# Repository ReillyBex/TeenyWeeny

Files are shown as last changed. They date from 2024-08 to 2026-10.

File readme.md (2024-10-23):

# TeenyWeeny

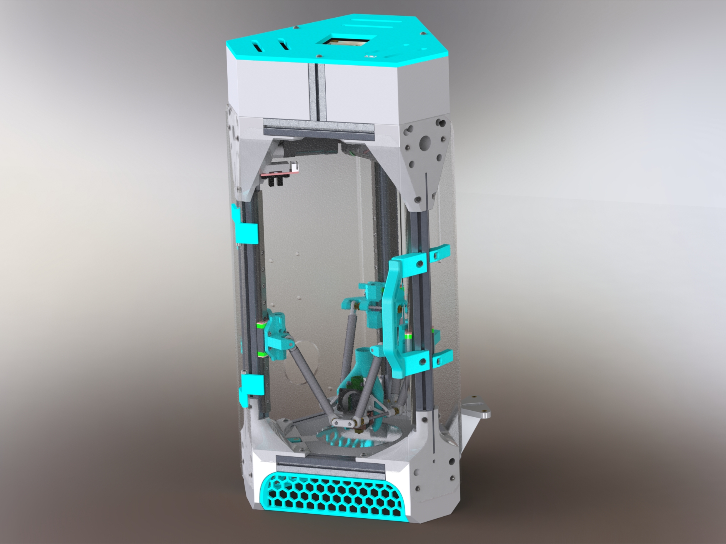
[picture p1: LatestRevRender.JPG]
Printer Render


A small form factor delta printer designed to be rigid and compact. I created most of the parts myself, but I also modified existing designs in the community. Credit is given below to the models I either used directly or modified. 

Print volume is 75mm diameter circle x ~120mm in Z. Arm Length is 85mm. Delta Radius is 38.1mm, Print_Radius is 37mm. Belt tension on the long side of the belt should be about 174Hz to reach spec load at spec length. Example graphs from Input Shaper are included below. 40k acceleration MZV is not too shabby! Smol delta go brrrrrrrr.          

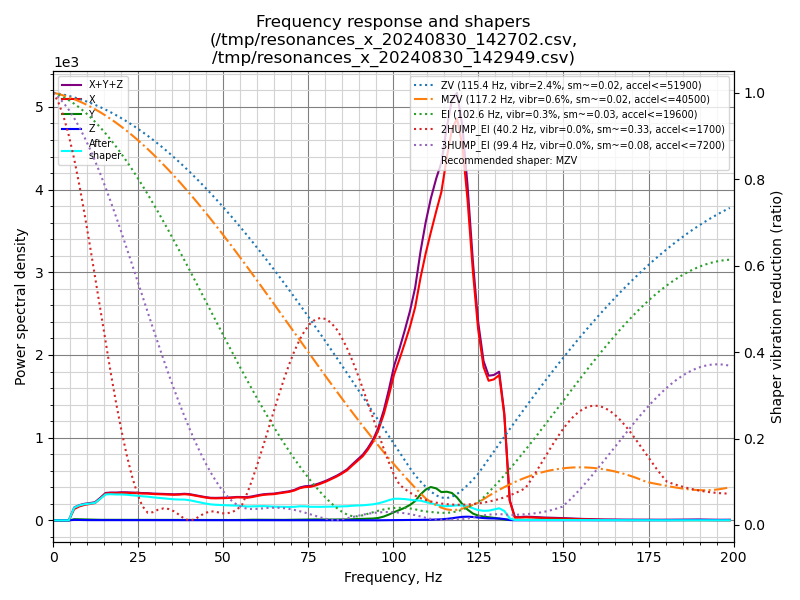
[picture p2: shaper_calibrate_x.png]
Shaper X
    
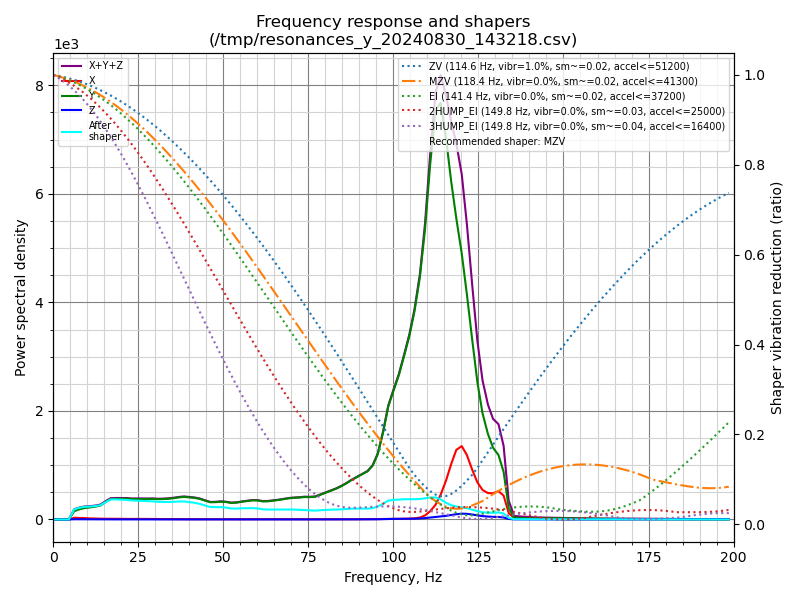
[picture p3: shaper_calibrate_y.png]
Shaper Y
          

Credit to models used in the CAD:  
https://www.printables.com/model/875189-min_sb01_80 for the stock effector design.    
https://github.com/clee/VoronBFI for the base BZI model I modified for use in Teeny Weeny.       
https://github.com/ApexArray/ApexClips for the Apex Clips used in the carriages.  
The MP Jet models are courtesy of Colphaer and Burgo, find them pinned in the Rolohaun discord Delta channel. 

Shoutout to models and designs used in the build:      
https://www.vorondesign.com/ for their designs and the starting point for pretty much all my work.      
https://github.com/KayosMaker/1515PanelClips for the 1515 panel clips.        
https://www.printables.com/model/857334-min-micro-delta-3d-printer for their work on small deltas and the discord community that helped me refine my design.      
https://www.printables.com/model/530995-v0-1515-extrusion-slot-cover/files for the 1515 slot covers.

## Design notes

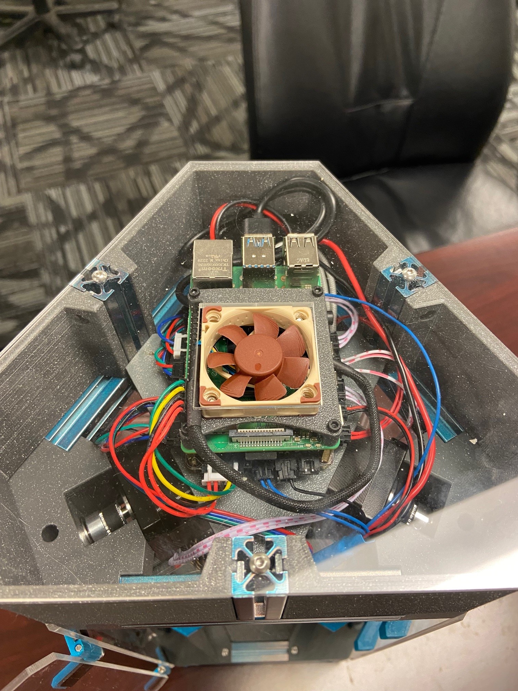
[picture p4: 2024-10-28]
Electronics Layout.jpg

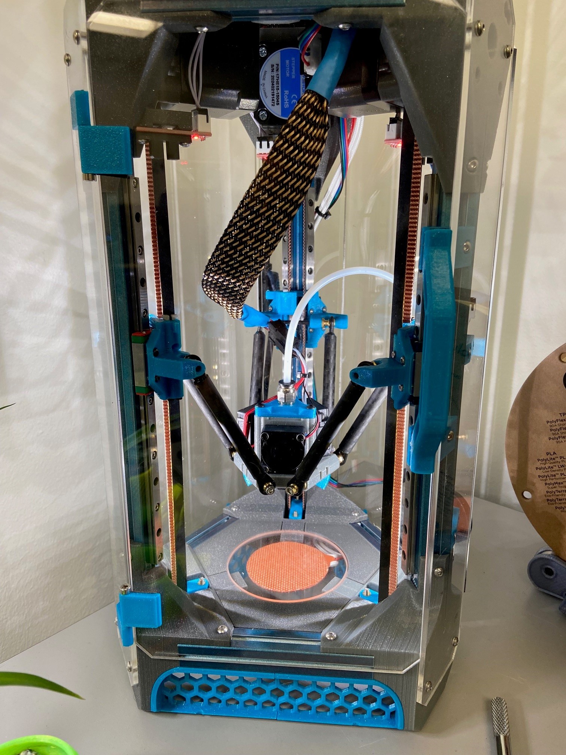
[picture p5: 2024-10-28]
Stock Config.jpg

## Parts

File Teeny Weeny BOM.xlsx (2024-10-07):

Teeny Weeny | Estimated Price | AliExpress | Amazon
Frame
3 x 250mm 1515 aluminum extrusion (might need to cut down from 300mm) | $15.00 |  | Amazon.com: MakerBeam XL Clear Anodized Beams 300x15x15mm 4 Pieces : Industrial & Scientific (https://www.amazon.com/MakerBeam-XL-Anodized-300x15x15mm-Pieces/dp/B06XJ4F9WW?hvadid=79852084166625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)
6 x 100mm 1515 aluminum extrusion | $25.00 |  | Amazon.com: MakerBeam XL Clear Anodized Beams 50x15x15mm (103374) 4 Pieces x 2 and 100x15x15mm (103385) 4 Pieces x 2 : Industrial & Scientific (https://www.amazon.com/MakerBeam-XL-Anodized-50x15x15mm-100x15x15mm/dp/B06XJ4FZ12?adgrpid=1341404752136090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)
3 x 50mm 1515 aluminum extrusion
Motion
POWGE GT2 6mm wide Belt 4 meters |  | https://s.click.aliexpress.com/e/_DBPBTXJ (https://www.aliexpress.com/item/902692789.html?pdp_ext_f=%7B%22sku_id%22%3A%2266484598505%22%7D) | Amazon.com: 5M GT2 Timing Belt, Upgrade Non-Slip Version, Width 6mm, Fit for 3D Printer and Most Belt Driven Printers : Automotive (https://www.amazon.com/dp/B08R93QQ8Z?ref=ppx_yo2ov_dt_b_product_details&th=1)
3 x 16T 5mm Bore Pulley |  | https://www.aliexpress.us/item/2251832808824051.html
6 x F623 flanged bearings (idler bearing stacks)
3 x F695 Bearings (Pack of 10 Raindew Recommended ) |  | https://s.click.aliexpress.com/e/_DeHjOz3
3 x Nema17 Any you prefer ( 48mm Max ) |  | https://s.click.aliexpress.com/e/_DmCB9SX | https://www.amazon.com/dp/B0B38GHRH8?psc=1&ref=ppx_yo2ov_dt_b_product_details
12 x MP Jet Joints (you need 2 packs of 6) |  |  | https://mpjet.com/shop/gb/ball-7-mm-dia/1286-375-ball-link-v1-type-7-mm-dia-m33-short.html
3 x 70mm length 3mm diameter carbon fiber rods for carriage joint pins (cut from longer rod) |  |  | Amazon.com: MECCANIXITY Carbon Fiber Rod, 3mm x 100mm for RC Plane DIY Tool Wing Tube Quadcopter Arm, Pack of 12 : Industrial & Scientific (https://www.amazon.com/dp/B0B6BWDQ67?ref=ppx_yo2ov_dt_b_product_details&th=1)
6 x 6mm ID 8mm OD 65mm long carbon fiber tubes for arms (Cut from longer tube) |  |  | Amazon.com: ARRIS 330mm 6mm x 8mm x 330mm Carbon Fiber Tubes Matte Surface 3K Roll Wrapped 100% Pure Pultruded Carbon Tubing for Quadcopter Multicopter (2PCS) : Industrial & Scientific (https://www.amazon.com/dp/B09X2Z385R?ref=ppx_yo2ov_dt_b_product_details&th=1)
6 x MGN7H 200mm Z2 preload linear rails |  | Linear Guide MGN7C MGN7H Rail Kit 440C Stainless Steel Miniature Slide Guideway Motion 1pc Rail with Carriage Set CNC 3D Printer - AliExpress 13 (https://www.aliexpress.us/item/3256801304880853.html?scm_id=1007.22922.271278.0&scm-url=1007.22922.271278.0)
Hardware ( Working in Progress )
82 - M3 x 8mm (a pack of 100 will probably be enough) |  | https://boltdepot.com/Metric_socket_cap_Stainless_steel_18-8_(A-2)_3mm_x_0.5mm
40 - M3 nuts (for screws into extrusion slots)
12 - M3 x 20mm for motor mounting
6 - M3 x 25mm for Effector Arms (Must be SHCS for clearances to work)
8 - M3x30mm for tensioners and door
Heatsets M3 X D5.0 X L4.0 ( I order 300 because you always need them :) ) |  | https://s.click.aliexpress.com/e/_DdVhkQl | uxcell knurled Insert Nuts, 120Pcs M3 x 4mm L x 5mm OD 3D Printing Brass Nuts Female Threaded Inserts Brass Heat Set Insert Embedment Nut: Amazon.com: Industrial & Scientific (https://www.amazon.com/dp/B09MCWTBCC?psc=1&ref=ppx_yo2ov_dt_b_product_details)
6 - M3NS square nuts for effector |  |  | HWM3D 25pcs M3nS - Thin M3 Square Nuts for PRUSA 3D Printers - A2 Stainless Steel - DIN562, Thickness 1.8mm: Amazon.com: Industrial & Scientific (https://www.amazon.com/dp/B0D6SP881V?ref=ppx_yo2ov_dt_b_product_details&th=1)
6 - M3 0.5mm shim washers for idler bearing stacks
Rubber feet |  |  | https://www.amazon.com/dp/B088HGQSZT?psc=1&ref=ppx_yo2ov_dt_b_product_details
M2.5 standoffs and fasteners for electornics and effector |  |  | DYWISHKEY 320 Pieces Male Female Hex Brass Spacer Standoff Screw Nut Assortment Kit (M2.5): Amazon.com: Industrial & Scientific (https://www.amazon.com/dp/B07MW5P8JH?ref=ppx_yo2ov_dt_b_product_details&th=1)
66 - M2 x 6 SHCS for rails and carriages |  | Bolt Depot - Metric socket cap, Stainless steel 18-8 (A-2), 2mm x 0.4mm (https://boltdepot.com/Metric_socket_cap_Stainless_steel_18-8_(A-2)_2mm_x_0.4mm)
58 - M2 nuts for rails
Extruder + Hotend
Dual Gear Extruder HGX-LITE-Extruder |  | https://s.click.aliexpress.com/e/_Dl5DEIV
Clone Bambu Hotend |  | https://s.click.aliexpress.com/e/_DFTGhVP
PC4-M10 pneumatic fitting |  | Amazon.com: PC4-M10 Male Straight Pneumatic PTFE Tube Push In Quick Fitting Connector for E3D-V6 Long-Distance Bowden Extruder 3D Printer (Pack of 10pcs) : Industrial & Scientific (https://www.amazon.com/dp/B07S1GLM8R?psc=1&ref=ppx_yo2ov_dt_b_product_details)
PC4-M6 pneumatic fitting |  | Amazon.com: PC4-M6 Straight Fitting 4mm Thread M6 Connector for 3D Printer (Pack of 10 pcs) : Industrial & Scientific (https://www.amazon.com/dp/B08BKJ1N6L?psc=1&ref=ppx_yo2ov_dt_b_product_details)
Nema 14 pancake stepper for extruder |  |  | Amazon.com: FYSETC 3D Printer Parts 36mm Motor Extruder Stepper Motor 1.8 Angle 0.35A 2 Phase Round Body with 47.2in Cable for Sherpa Mini/Orbite Extruder Ender 3 Pro V2 /Voro 2.4/Positro Project Accessories : Industrial & Scientific (https://www.amazon.com/dp/B099JMJNH2?psc=1&ref=ppx_yo2ov_dt_b_product_details)
BED
Borosilicate glass disk | $23.18 | https://www.mcmaster.com/8477K88
24V 30W 50mm diameter silicone heating pad (Keenovo custom order) | $50.00 | Contact Us_Custom Flexible Heating Elements, Silicone Heater, Kapton Heater-Keenovo.com (https://www.keenovo.com/contact/us.html)
Electronics
24v 6amp AC Adapter |  | https://s.click.aliexpress.com/e/_DdGr7Hd
Optical Endstop |  | https://s.click.aliexpress.com/e/_DF2pjnD
BTT Pico |  | https://s.click.aliexpress.com/e/_DClRklL | Amazon.com: BIGTREETECH SKR PICO V1.0 Control Board Integrated 4 Axis TMC2209 UART Stepper Motor Driver Compatible with Raspberry Pi Online Printing for Voron V0 V0.1 3D Printer Motherboard : Industrial & Scientific (https://www.amazon.com/dp/B09MYKL9MP?ref=ppx_yo2ov_dt_b_product_details&th=1)
SBC (any Raspberry Pi should work)
2510 5v ball bearing fan for hotend ( I recommend Delta )
3010 24v GDstime Layer Cooling |  | https://s.click.aliexpress.com/e/_DCciStb
2x8 molex microfit 3.0 connector for effector umbilical |  |  | Molex Micro-Fit 3.0 Dual Row (8 Circuits) Male & Female Receptacle Plug, w/Terminal sockets, (Pack of 1 Complete Set): Amazon.com: Industrial & Scientific (https://www.amazon.com/dp/B07997NH2Q?psc=1&ref=ppx_yo2ov_dt_b_product_details)
4010 fan for Raspberry Pi cooling (optional) |  |  | Amazon.com: Noctua NF-A4x10 5V, Premium Quiet Fan, 3-Pin, 5V Version (40x10mm, Brown) : Electronics (https://www.amazon.com/Noctua-Cooling-Bearing-NF-A4X10-FLX-5V/dp/B00NEMGCIA)
CPAP Driver Board (IF using CPAP toolhead) |  | High Speed Turbine Fan with Nidec Brushless Motor and Built-in Drive for Sweeper and Vacuum Cleaner - AliExpress 1420 (https://www.aliexpress.us/item/3256805751725080.html)
Roborock Blower Fan |  | Ldee5bgs173tw01|roborock S50 S51 S52 S55 Motor Replacement - Xiaomi Mi Robot Sdjqr01rr Parts (aliexpress.us) (https://www.aliexpress.us/item/3256804036608448.html)
TOTAL CAD | $113.18
TOTAL USD | #NAME?

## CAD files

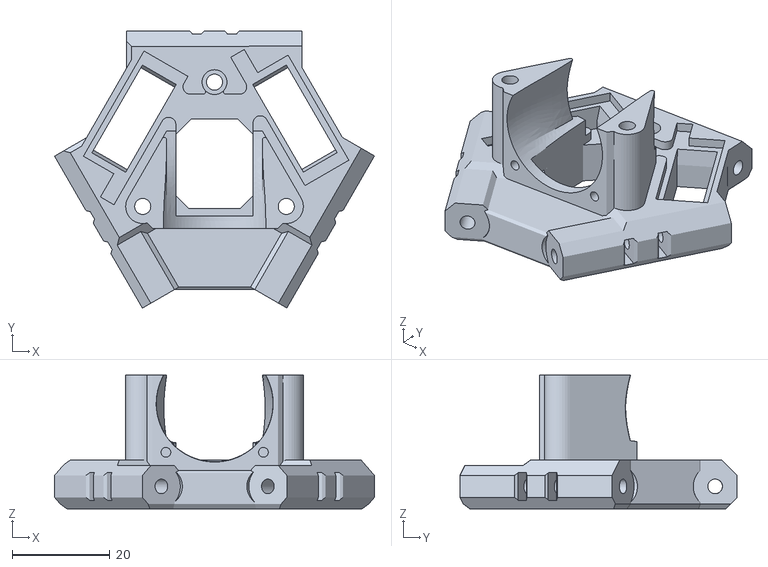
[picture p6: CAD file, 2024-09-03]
STL/Bambu SB Effector/MIN_EFFECTOR_M3X30_3010_BAMBU_MainPlate.STL
65.6 x 56.9 x 27.4

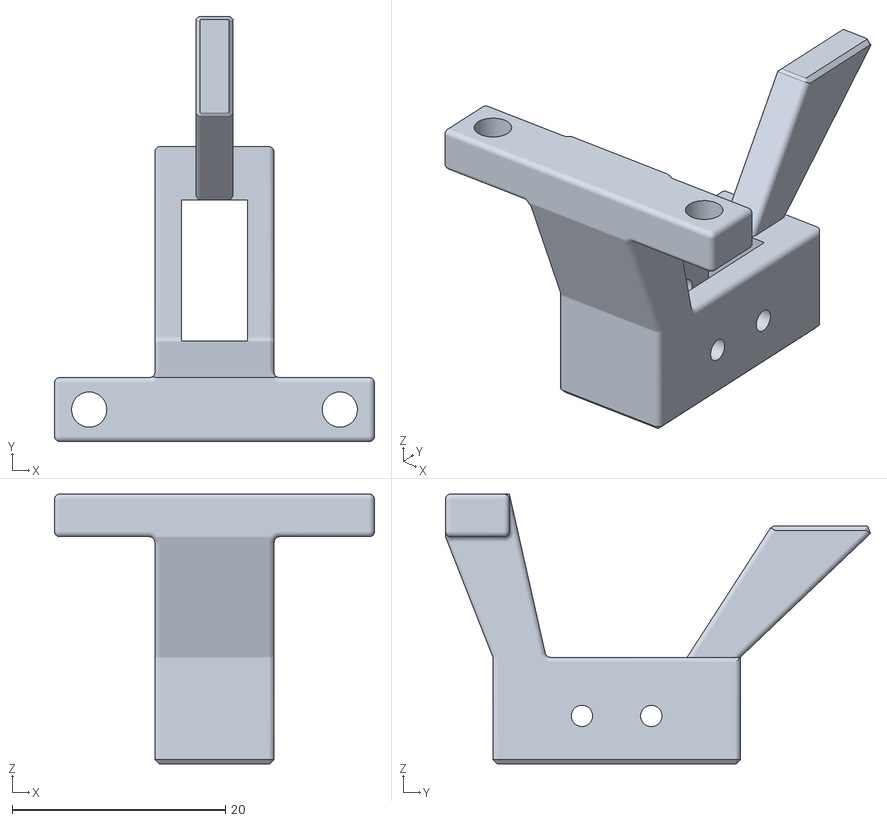
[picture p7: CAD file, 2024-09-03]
STL/Bambu SB Effector/Probe_Mount.STL
30.0 x 39.9 x 25.3

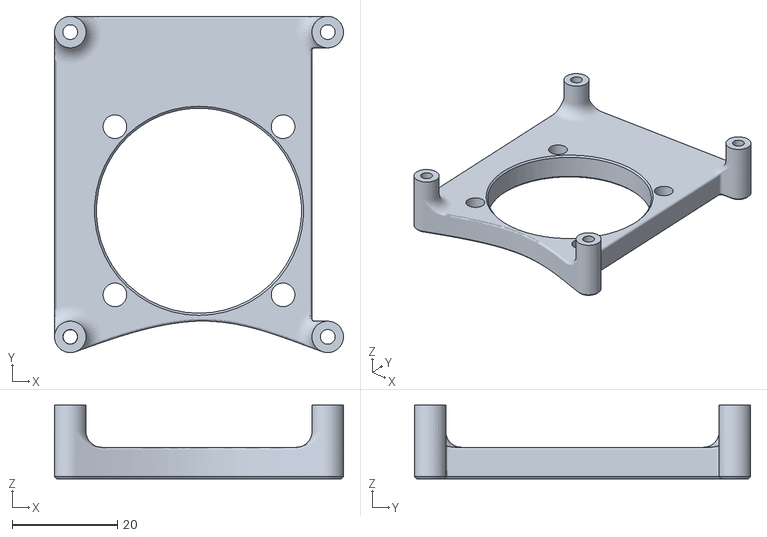
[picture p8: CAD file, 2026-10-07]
STL/Electronics/4010_RPi_FanMount_Heatset.STL
55.0 x 64.0 x 14.0

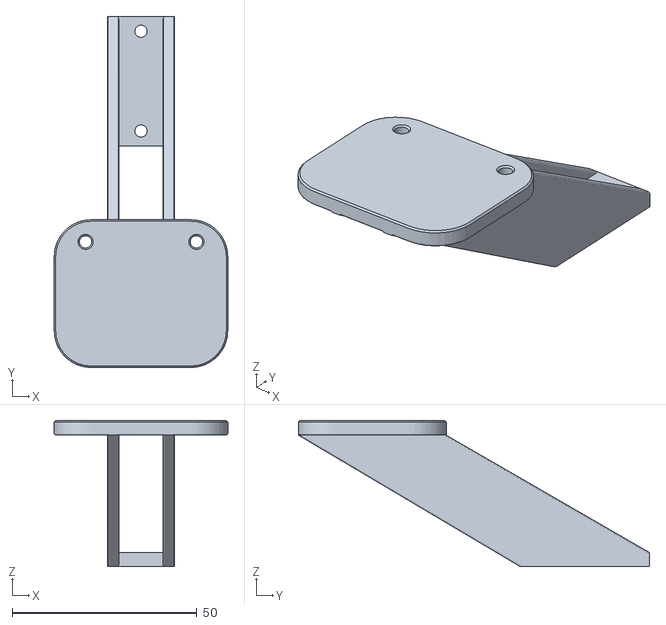
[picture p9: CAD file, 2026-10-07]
STL/MISC/Jetpack_Mount_Taller.STL
47.0 x 95.0 x 39.5

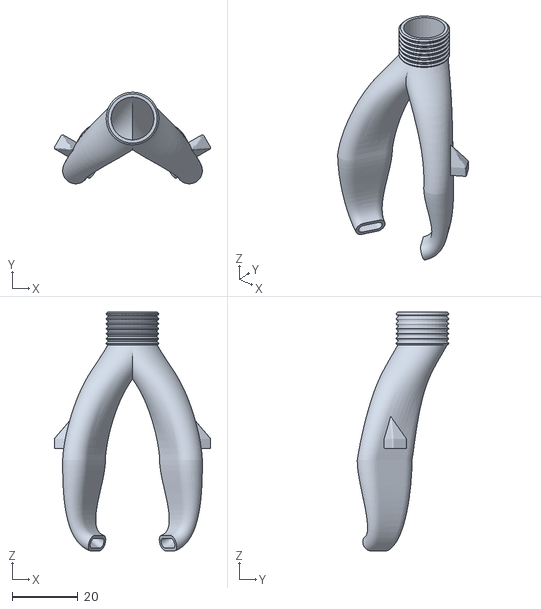
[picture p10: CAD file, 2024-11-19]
STL/Motion/CPAP Ducts.STL
47.5 x 27.8 x 72.6

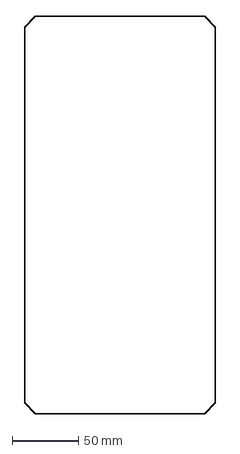
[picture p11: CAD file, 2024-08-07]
STL/Panel DXFs/Side_Door_Panel_x3.DXF
143.8 x 299.2 mm

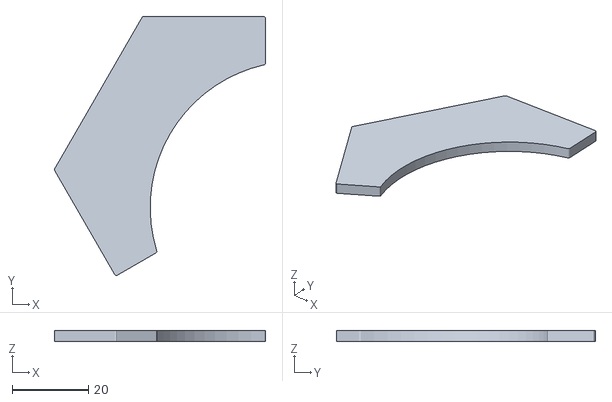
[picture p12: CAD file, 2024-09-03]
STL/Panels/BedPanel_1_x3.STL
55.3 x 67.8 x 3.00

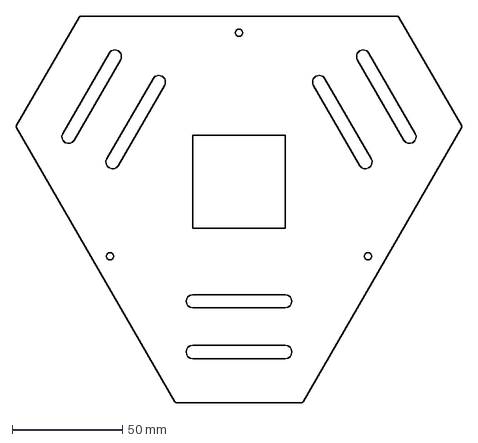
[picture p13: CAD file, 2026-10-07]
STL/Panels/Panel DXFs/TopPanel_Cutouts.DXF
201.8 x 175.1 mm

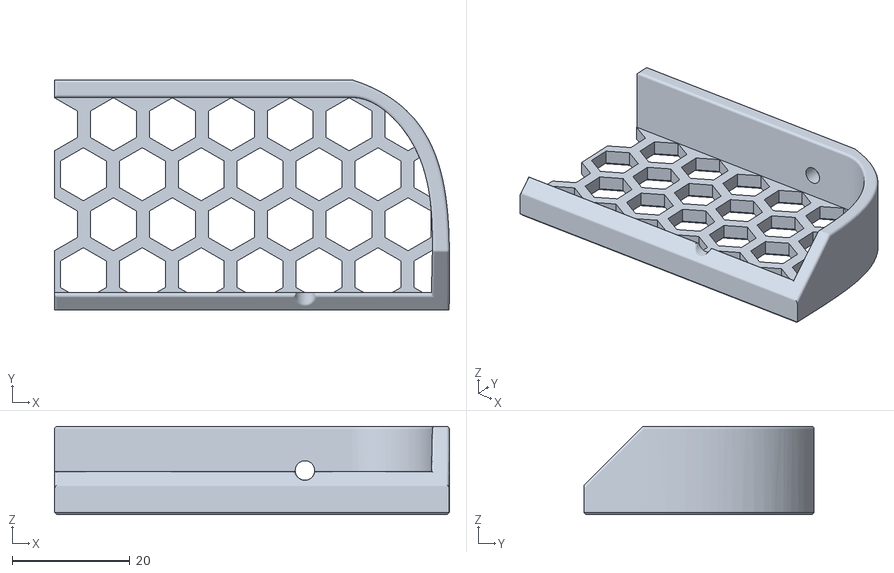
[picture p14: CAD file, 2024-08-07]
STL/Skirts/[a]_Skirt_Half_x3.STL
67.0 x 39.1 x 15.0

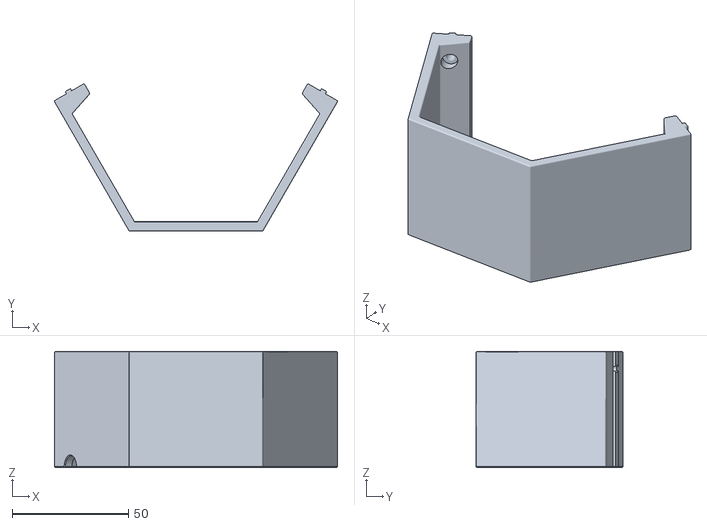
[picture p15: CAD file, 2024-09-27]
STL/Structure/TopHat_CPAP_Wires.STL
121.9 x 63.3 x 50.0

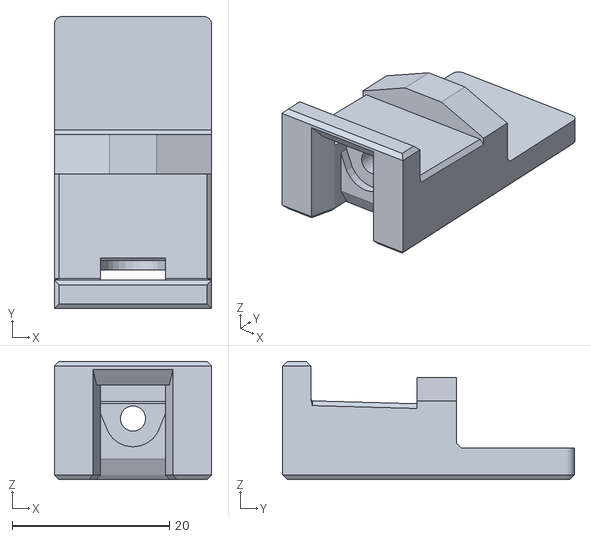
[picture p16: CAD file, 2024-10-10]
STL/Tools/MP Jet Joint Filing Jig V2.stl
20.0 x 37.1 x 15.0

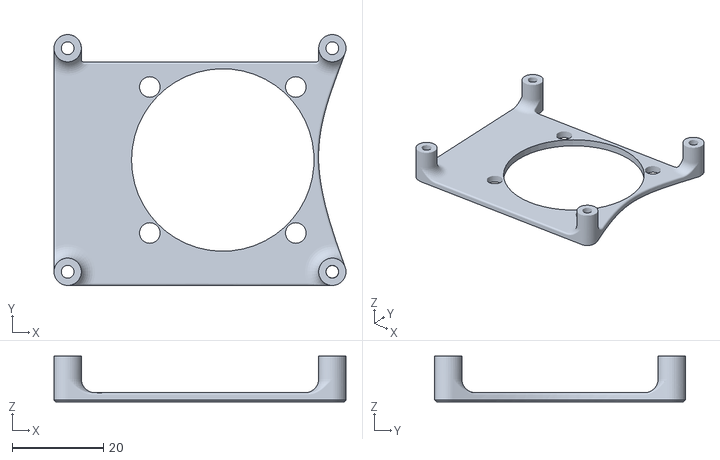
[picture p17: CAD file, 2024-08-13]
STL/Electronics/4010_RPi_FanMount.STL
64.0 x 55.0 x 10.0

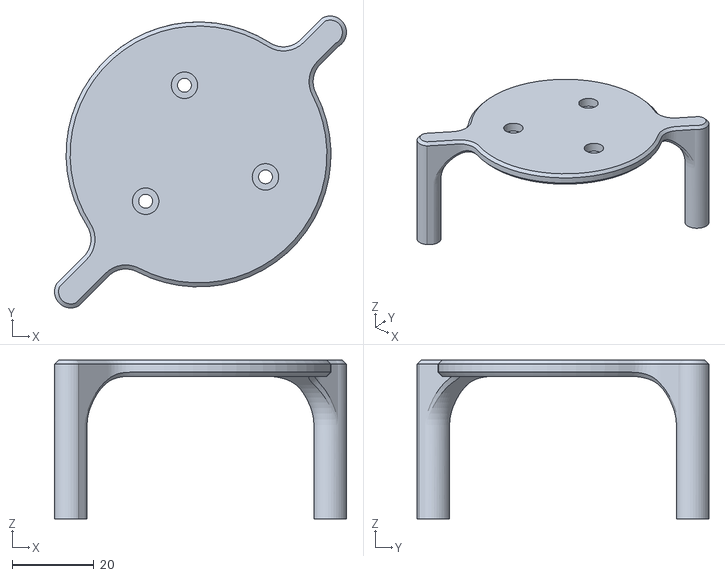
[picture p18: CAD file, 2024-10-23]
STL/MISC/mount_plate_no_logo.STL
71.6 x 71.6 x 39.0

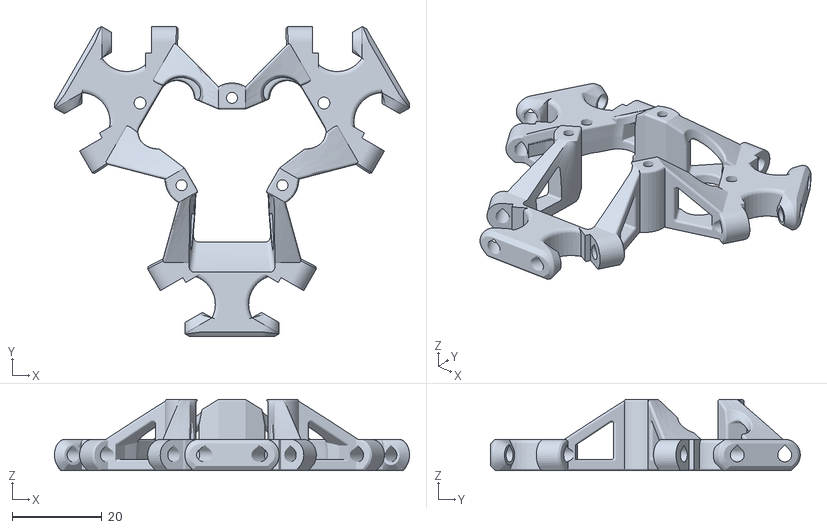
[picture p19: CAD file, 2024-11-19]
STL/Motion/CPAP Effector Plate.STL
79.2 x 69.1 x 15.9

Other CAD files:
STL/Panels/BedPanel.STL
STL/Panels/Panel DXFs/CPAP_Side_Panel.DXF
STL/Skirts/[a]_Skirt_Half_Mirror_x3.STL
STL/Structure/Foot_Double_Cable_Routing.STL
STL/Bambu SB Effector/MIN_EFFECTOR_M3X30_3010_BAMBU_CoolingDucts.STL
STL/Bambu SB Effector/MIN_EFFECTOR_M3X30_3010_BAMBU_HotendMount.STL
STL/Bambu SB Effector/MIN_EFFECTOR_M3X30_3010_BAMBU_MolexMount.STL
STL/Bambu SB Effector/MIN_EFFECTOR_M3X30_3010_BAMBU_PneumaticMount.STL
STL/Bambu SB Effector/MIN_EFFECTOR_M3X30_3010_BAMBU_Standoff.STL
STL/Electronics/ElectronicsMount.STL
STL/Electronics/RPi_Standoff_x4.STL
STL/MISC/1515_slot_cover.stl
STL/MISC/Sherpa_Mini_Mount_Taller.STL
STL/MISC/[a]_Matchstick_Mount_x4.STL
STL/MISC/adapter_plate.stl
STL/Motion/Apex_Clip_x6.stl
STL/Motion/EffectorStrainRelief.STL
STL/Motion/HotendDuct.STL
STL/Motion/[a]_LinearCarriage_Ground MP Jets_x3.STL
STL/Motion/[a]_LinearCarriage_x3.STL
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

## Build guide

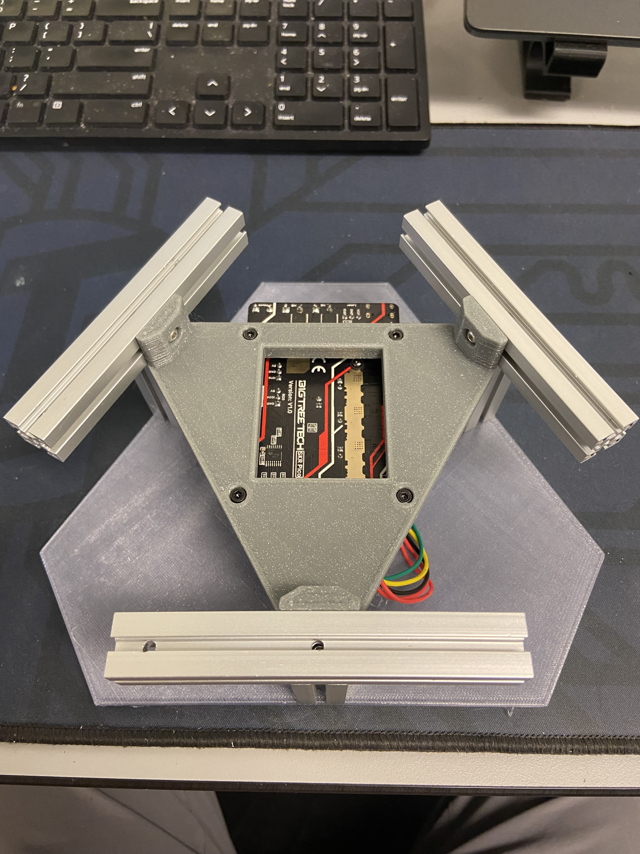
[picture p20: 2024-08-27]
Assembly Photos/6 Use top panel to align extrusions before tightening.jpeg

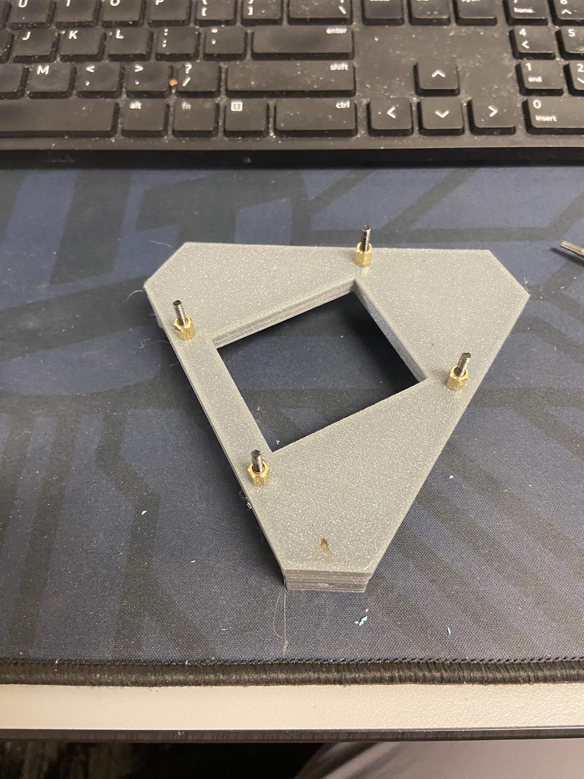
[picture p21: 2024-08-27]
Assembly Photos/1 Standoff Prep.jpeg

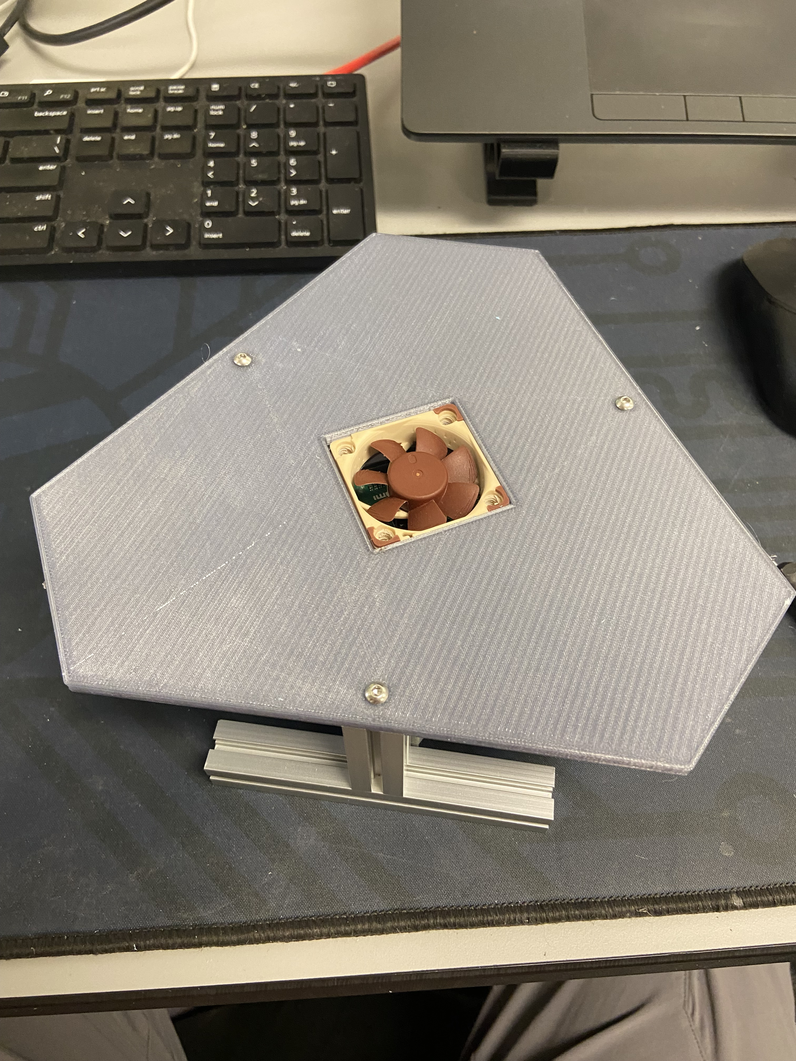
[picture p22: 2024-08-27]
Assembly Photos/7 Finished electronics assembly.jpeg

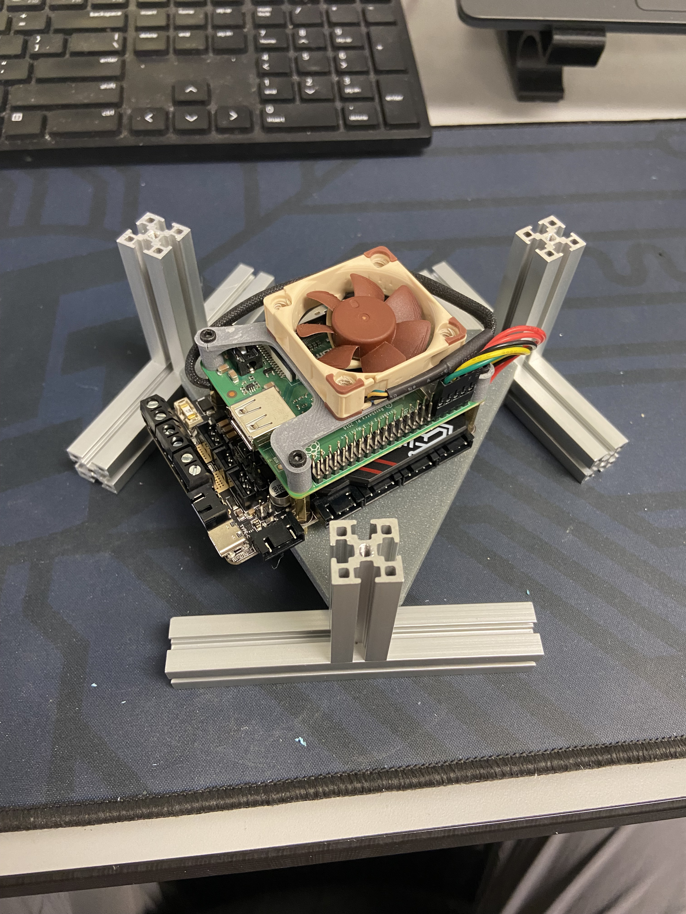
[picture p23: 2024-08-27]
Assembly Photos/5 Add extrusions keep loose.jpeg

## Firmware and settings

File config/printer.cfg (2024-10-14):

[mcu]
serial: /dev/ttyAMA0    #UART serial ID
#serial: /dev/serial/by-id/usb-Klipper_rp2040_45503571270D6318-if00    #USB serial ID
restart_method: command    #Comment/delete this line if you are using USB, or change the method to be "arduino"

[printer]
kinematics: delta
max_velocity: 500
max_accel: 41300                # This value is from my Input Shaper tests. Drop to a lower value or tune IS yourself. 
max_z_velocity: 500
max_z_accel: 41300
delta_radius: 38.1             # This is nominal value from CAD. This will change with a delta_calibrate. 
print_radius: 37
minimum_z_position: -5

[delta_calibrate]
radius: 37
horizontal_move_z: 20

[gcode_arcs]
resolution: 0.1

[endstop_phase]    #Use included macro to tune this

[input_shaper]     #Tune this yourself using the KUSBA or the BTT adxl345 V2.0 (Both configs included. KUSBA only works for the SB effector plate, the BTT chip is for the CPAP effector)
shaper_freq_x: 117.2
shaper_type_x: mzv
shaper_freq_y: 118.4
shaper_type_y: mzv

#############################################################
#~~~~~~~~~~~~~~~~~~~~~  STEPPERS  ~~~~~~~~~~~~~~~~~~~~~~~~~~#
#############################################################

#Front left tower
[stepper_a]
step_pin: gpio14
dir_pin: !gpio13
enable_pin: !gpio15
microsteps: 32
rotation_distance: 32
endstop_pin: ^gpio4
position_endstop: 125
homing_speed: 50
arm_length: 85.0             # Highly recommend measuring the center to center distance of the pins on the arm jig and using that value here. 

[tmc2209 stepper_a]
uart_pin: gpio9
tx_pin: gpio8
uart_address: 3
run_current: 0.8
interpolate: True
sense_resistor: 0.110
stealthchop_threshold: 0 

#Front right tower
[stepper_b]
step_pin: gpio11
dir_pin: !gpio10
enable_pin: !gpio12
microsteps: 32
rotation_distance: 32
endstop_pin: ^gpio3

[tmc2209 stepper_b]
uart_pin: gpio9
tx_pin: gpio8
uart_address: 0
interpolate: True
run_current: 0.8
sense_resistor: 0.110
stealthchop_threshold: 0 

#Back tower
[stepper_c]
step_pin: gpio6
dir_pin: !gpio5
enable_pin: !gpio7
microsteps: 32
rotation_distance: 32
endstop_pin: ^gpio25

[tmc2209 stepper_c]
uart_pin: gpio9
tx_pin: gpio8
uart_address: 2
interpolate: True
run_current: 0.8
sense_resistor: 0.110
stealthchop_threshold: 0 

#############################################################
#~~~~~~~~~~~~~~~~~~~~~~  HEATERS  ~~~~~~~~~~~~~~~~~~~~~~~~~~#
#############################################################

[extruder]
step_pin: gpio19
dir_pin: gpio28
enable_pin: !gpio2
microsteps: 32
gear_ratio: 50:17
rotation_distance: 13.25
nozzle_diameter: 0.2                    # Check your nozzle size!
filament_diameter: 1.75
heater_pin: gpio23
sensor_type: EPCOS 100K B57560G104F
sensor_pin: gpio27
control: pid 
pid_kp: 44.411
pid_ki: 19.738
pid_kd: 24.981
min_temp: 0
max_temp: 300
min_extrude_temp: 0
max_extrude_cross_section:2
pressure_advance: 0.5

[tmc2209 extruder]
uart_pin: gpio9
tx_pin: gpio8
uart_address: 1
interpolate: True
run_current: 0.6
sense_resistor: 0.110
stealthchop_threshold: 0 

[heater_bed]
heater_pin: gpio21
sensor_type: EPCOS 100K B57560G104F
sensor_pin: gpio26
control: pid
pid_kp: 49.206
pid_ki: 2.262
pid_kd: 267.555
min_temp: 0
max_temp: 130

#############################################################
#~~~~~~~~~~~~~~~~~~~~~~~~  FANS  ~~~~~~~~~~~~~~~~~~~~~~~~~~~#
#############################################################

# RoboRock CPAP part cooling (needs klipper expander to work)
[fan]
pin: expander:PA3
off_below: 0.15
kick_start_time: 0.2

#Part_Cooling (SB effector)
#[fan]
#pin: gpio17

[heater_fan hotend_fan]
pin: gpio18
heater: extruder
heater_temp: 50.0

#Host/electronics compartment fan (vent up and out)
[output_pin Electronics_Fan]
pin: gpio24
value: 1    #Always on to improve thermals.... hopefully! See the temperature fan included below for a temperature controlled version. 

#[temperature_fan RPi_fan]
#pin: gpio24
#sensor_type: temperature_host
#control: watermark
#max_delta: 5
#min_temp: 0
#max_temp: 60

#############################################################
#~~~~~~~~~~~~~~~~~~~~~~~~  MISC  ~~~~~~~~~~~~~~~~~~~~~~~~~~~#
#############################################################

[output_pin Matchsticks]
pin: expander:PA1    #Or gpio20 if not using expander
value: 1

# Probe for the SB effector. Manual calibration is usually preferred. 
[probe]
pin: expander:PA7    #Use gpio16 if you don't have a klipper expander
z_offset:12.550      #Be sure to do your own probe_calibrate
speed: 2
samples: 5
samples_tolerance: 0.05

#############################################################
#~~~~~~~~~~~~~~~~~~~~~~  Includes  ~~~~~~~~~~~~~~~~~~~~~~~~~#
#############################################################

[include mainsail.cfg]
[include macros.cfg]
[include klipperExpander.cfg]
#[include KUSBA.cfg]
#[include adxl345-v2.0.cfg]

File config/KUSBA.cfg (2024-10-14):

[mcu adxl]
serial: /dev/serial/by-id/usb-Anchor_Rampon-if00

[adxl345]
cs_pin: adxl:CS

[resonance_tester]
accel_chip: adxl345
accel_per_hz: 100
probe_points:
   0,0,80
# Edit the above line with the correct probe points location. I recommend the center of your bed for X & Y, 20 for Z.
# For 350 mm printers: 175,175,20
# For 300 mm printers: 150,150,20
# For 250 mm printers: 125,125,20
# For 120 mm printers: 60,60,20

# More info: https://www.klipper3d.org/Config_Reference.html#adxl345

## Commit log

2024-08-09 updated cad to have fasteners and other fixes
2024-08-13 updated parts
    [4010_RPi_FanMount.STL, BedPanel.DXF, BedPanel.STL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]
2024-08-19 Added electronics assembly photos
2024-08-27 updated panels, matchstick mounts
    [Extruder_Side_Panel.DXF, Side_Door_Panel_x2.DXF, [a]_Matchstick_Mount_x4.STL]
2024-08-27 updated cad
2024-09-03 updated foot geometry
    fixed cooling duct interferences
    [BedPanel.DXF, BedPanel_1_x3.STL, Foot_Cable_Routing.STL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]
2024-09-03 updated cad of foot
2024-09-03 updated effector mount, added ndn and nut tool, added probe mount
    [MIN_EFFECTOR_M3X30_3010_BAMBU_MainPlate.STL, Probe_Mount.STL, [a]_LinearCarriage_x3.STL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]
2024-09-03 updated cad of effector and probe mount
2024-09-05 updated gitignore, config upload
    [macros.cfg, printer.cfg]
2024-09-06 cleaned up config, added example shaper graphs
    [macros.cfg, printer.cfg]
2024-09-06 massive config fix, added klipper expander to build
    [printer.cfg]
2024-09-06 stock config doesn't assume klipper expander now
    [macros.cfg, printer.cfg]
2024-09-27 general update
    [CPAP_Side_Panel.DXF, R4.V3.-UfO-N-AtOR.top.entry.blank.2.STL, Sherpa_Mini_Mount.STL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]
2024-09-27 returned stock effector to CAD
2024-09-27 cleaned up CAD a bit for .step export
2024-09-27 cleaned up stls
    [100mm_BlindJoint_Jig.STL, 1515_slot_cover.stl, 4010_RPi_FanMount.STL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]
2024-10-07 general updates, working on CPAP effector beta files
    [CPAP Driver Drill Guide.STL, CPAP Ducts.STL, CPAP Effector Plate Shoulder Bolts.STL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]
2024-10-09 beta testing effector plate
    [CPAP Effector Plate Tear Drop Holes.STL, CPAP Effector Plate.STL]
2024-10-10 reorganized .stl files, new render with CPAP effector
    [CPAP Ducts.STL, CPAP Effector Plate Shoulder Bolts.STL, CPAP Effector Plate Tear Drop Holes.STL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]
2024-10-11 updated effector plate. new render, new step file.
    [CPAP Effector Plate Tear Drop Holes.STL, CPAP Effector Plate.STL]
2024-10-14 updated config section
    [KUSBA.cfg, adxl345-v2.0.cfg, klipperExpander.cfg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]
2024-10-23 updated CAD for CAZA
    [adapter_plate.stl, mount_plate_no_logo.STL]
2024-11-13 updated things slightly
    [CPAP Ducts.STL, CPAP Effector Plate.STL]
2024-11-19 updated CPAP effector geometry and layout
    [CPAP Ducts.STL, CPAP Effector Plate.STL, HotendDuct.STL]
2024-11-19 testing ducts
    [CPAP Ducts.STL, CPAP Effector Plate.STL]
